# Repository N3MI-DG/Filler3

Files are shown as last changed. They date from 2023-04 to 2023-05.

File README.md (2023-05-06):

# Filler3
 Open source can filler built from 3D printer, 3D printed and common home brewing items.

 Credits to <a href="https://www.youtube.com/channel/UCIIYTzYpd8D7y816diZB0Dw">HarryBrew69</a> for coming up with the idea of using an Arduino to run a can filler and sense fill level via analog inputs. And <a href="https://github.com/kloon/OpenBeerFiller">kloon</a> for his original implimentation of Harry's idea.

<a href="BOM.csv">BOM</a><br/>
<a href="/Build/">The Build</a><br/>
<a href="/Photos/">Build Photos</a><br/>
<a href="/firmware/">Firmware</a><br/>
<a href="/CQ-SRC/">CadQuery</a><br/>
<br/>

## Method of operation
<p>
    When plugged in the can filler will move the servo to the <b>SERVO_POS_IDLE</b> position, make sure the gas solenoid is disabled and raise the gantry to its home position and wait for user input.
    <br/><br/>
    Pressing the button will activate the filling process. 
    <br/><br/>
    The gantry will move to the <b>PRE_PURGE_POSITION</b> and activate the gas solenoid for the <b>PRE_PURGE_DURATION</b>.
    <br/><br/>
    After purging the gantry will move to the <b>FILL_POSITION</b>, the servo will move to the <b>SERVO_POS_FILL</b> position and the LED will start "breathing" to indicate the can is filling. 
    <br/><br/>
    If using <b>POSITIVE_PRESSURE</b> mode, the purge cap should be touching the can while filling. If not using the <b>POSITIVE_PRESSURE</b> mode, the purge cap should be positioned as close to the can as possible without touching. 
    <br/><br/>
    While filling the sensor wire is constantly being read and checking if the analog input has gone past the <b>SENSOR_TRIGGER</b> value.
    The <b>SENSOR_TRIGGER</b> value will need to be tuned if canning non still liquids.
    <br/><br/>
    Once full the servo will move back to the <b>SERVO_POS_IDLE</b> position. While the can is full and the gantry is down, the combination of <b>POSITIVE_PRESSURE</b> and <b>POST_PURGE_DURATION</b> settings will determine what happens next.
    <br/><br/>
    If using <b>POSITIVE_PRESSURE</b> mode, the LED will start "blinking" to indicate the can is full and wait for the button to be pressed before moving to the next position. This behaviour is to allow the user to grab hold of the can before the gantry moves to the next position. If the gantry moves while the purge cap is touching the can and the can is not held in position things can get very messy.
    <br/><br/>
    If <b>POSITIVE_PRESSURE</b> mode is disabled, the gantry will automatically move to the next position once the can is full. 
    <br/><br/>
    If a <b>POST_PURGE_DURATION</b> value has been set the gantry will move to the <b>POST_PURGE_POSITION</b> and activate the purge solenoid for the <b>POST_PURGE_DURATION</b> before moving the gantry back to the home position.
    <br/><br/>
    If no <b>POST_PURGE_DURATION</b> is set the gantry will move directly to the home position after filling.
    <br/><br/><br/>
    <b>NOTE: IF THE BUTTON IS PRESSED ANY TIME OTHER THAN WHILE THE GANTRY IS AT ITS HOME POSITION OR WHILE THE LED IS "BLINKING" IT IS TREATED AS AN EMERGENCY STOP AND WILL RESET THE FILLER.</b>
</p>
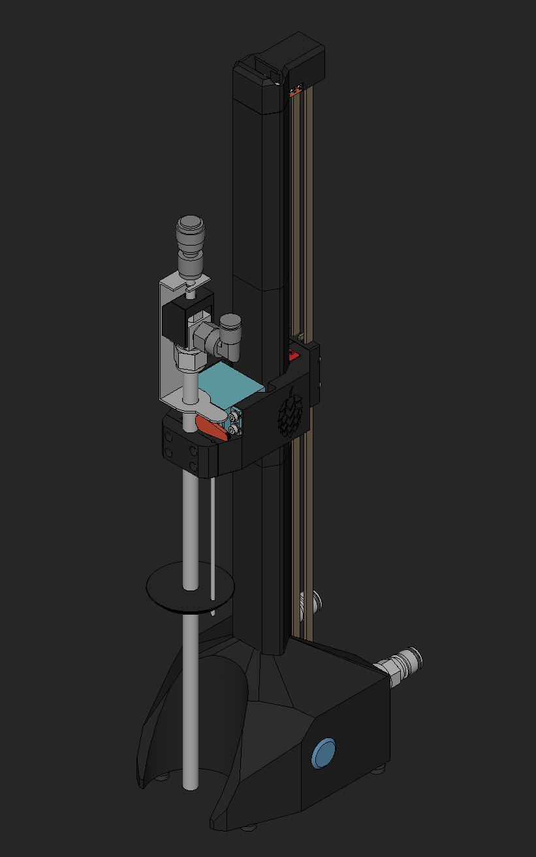
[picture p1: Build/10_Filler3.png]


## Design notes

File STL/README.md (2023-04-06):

# Printed Parts

1x Base.stl<br/>
1x Car Stop.stl<br/>
1x Carriage.stl<br/>
1x Condensation Cover.stl<br/>
1x DFU Helper.stl<br/>
1x Filler Mount Front.stl (PETG Recommended for clamping purpose.)<br/>
1x Filler Mount Left.stl (PETG Recommended for clamping purpose.)<br/>
1x Filler Mount Right.stl (PETG Recommended for clamping purpose.)<br/>
4x Foot.stl<br/>
1x Handle Stop.stl<br/>
1x Idle Stop.stl<br/>
1x Motor Mount.stl (PETG/ABS/ASA Recommended for heat absorbtion.)<br/>
1x PCB Spacer.stl<br/>
1x Purge Cap.stl (FLEXIBLE Required to push fit.)<br/>
2x Tube Section.stl<br/>

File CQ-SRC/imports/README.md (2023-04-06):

Note: Some files were modified from their originals to either simplify them or suit this project. The URLs listed are the original source.
<br/>

* 17HS08-1004S.stp : https://grabcad.com/library/17hs08-1004s-4-lead-nema-17-stepper-motor-1<br/>
* ball_lock.dxf : David Gray / Filler3<br/>
* dfu_a.dxf : David Gray / Filler3<br/>
* dfu_b.dxf : David Gray / Filler3<br/>
* EBB42.step : https://github.com/bigtreetech/EBB/blob/master/EBB%20CAN%20V1.1%20(STM32G0B1)/EBB42%20CAN%20V1.1/3D/BIGTREETECH%20EBB42%20CAN%20V1.1.step<br/>
* filler_clearance.dxf : David Gray / Filler3<br/>
* filler_tube.step : David Gray / Filler3<br/>
* hop_cone.step : David Gray / Filler3<br/>
* MG996R.step : https://grabcad.com/library/tower-pro-mg-996r-motor-3d-model-1<br/>
* MGN12_RAIL_400.step : https://grabcad.com/library/mgn12-lineer-guide-1<br/>
* MGN12H_CAR.step : https://grabcad.com/library/mgn12-lineer-guide-1<br/>
* pulley.dxf : David Gray / Filler3<br/>
* servo_arm.step : David Gray / Filler3<br/>
* Solenoid_Valve_1_4.stp : https://grabcad.com/library/china-solenoid-valve-1-4-for-reference-1<br/>
* SPDT.stp : https://grabcad.com/library/microswitch-13<br/>
* v_inner_a.dxf : David Gray / Filler3<br/>
* v_inner_b.dxf : David Gray / Filler3<br/>
* v_inner_c.dxf : David Gray / Filler3<br/>
* v_inner_d.dxf : David Gray / Filler3<br/>
* V_tube_body.dxf : David Gray / Filler3<br/>
* V-Slot 20x20.dxf : https://github.com/richard-scott/OpenBuilds<br/>

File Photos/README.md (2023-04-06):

# Photos

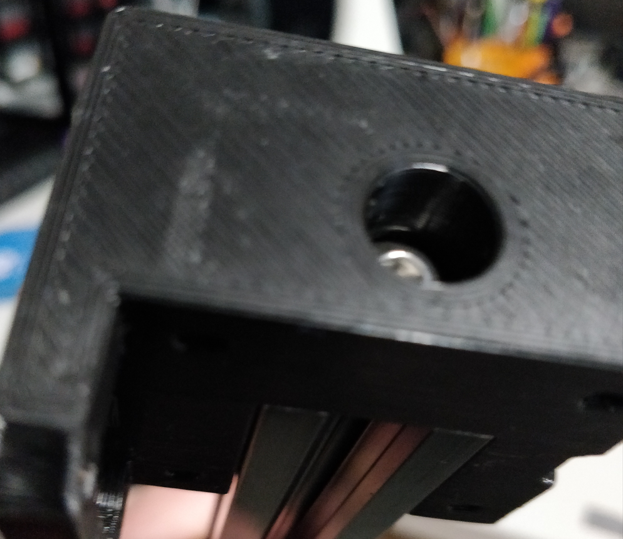
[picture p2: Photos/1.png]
<br/>
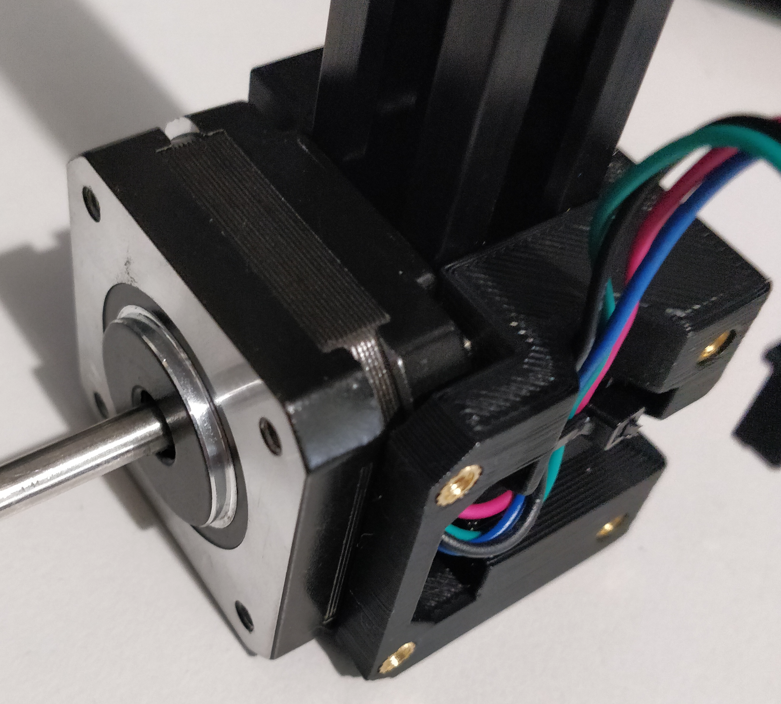
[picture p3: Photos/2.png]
<br/>
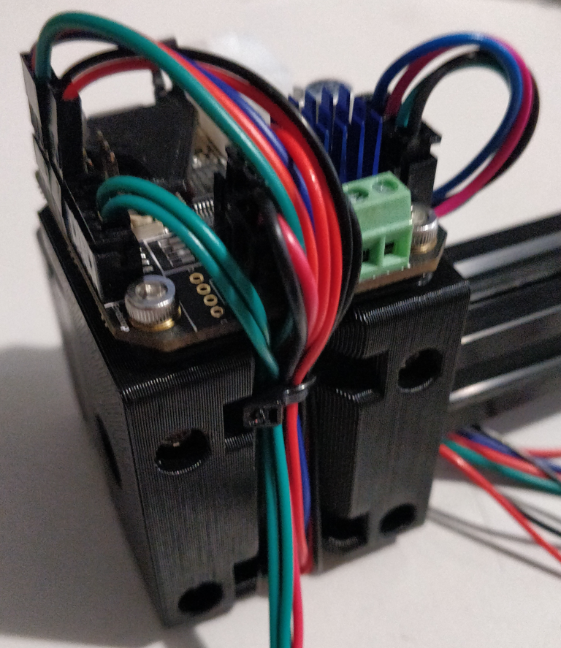
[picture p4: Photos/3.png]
<br/>
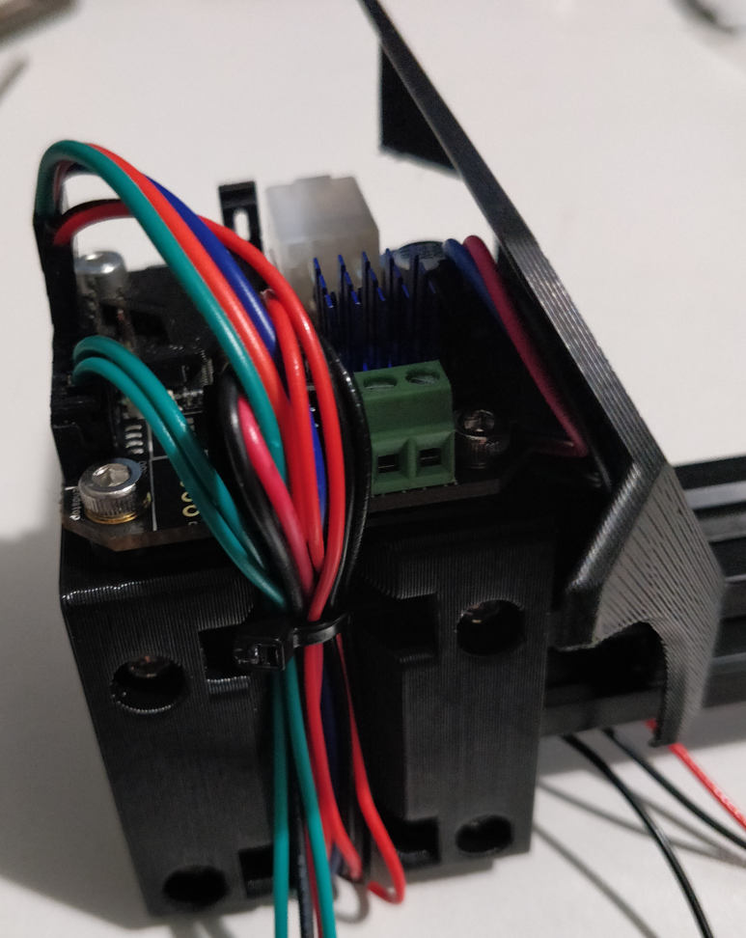
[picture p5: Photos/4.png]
<br/>
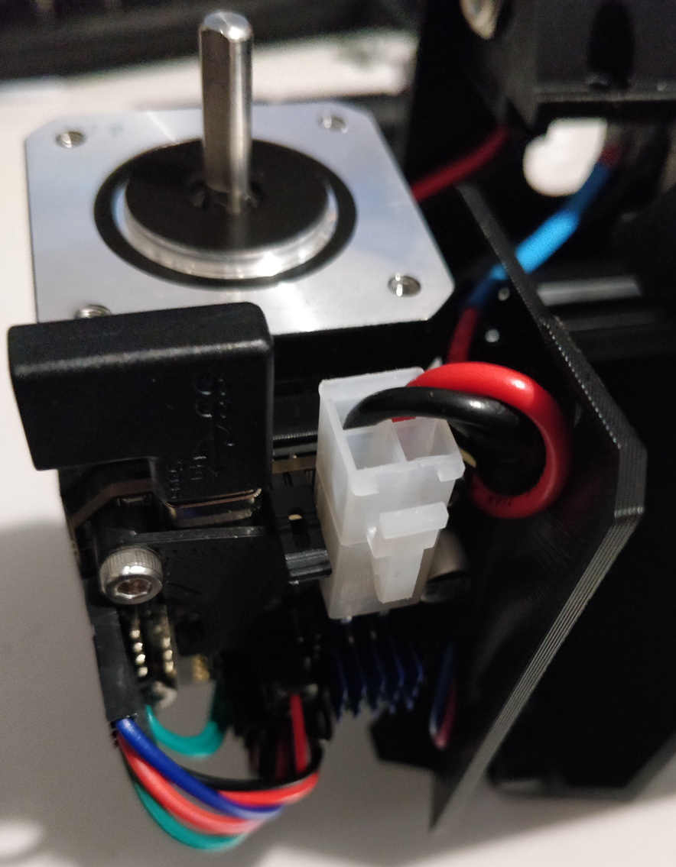
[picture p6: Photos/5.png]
<br/>
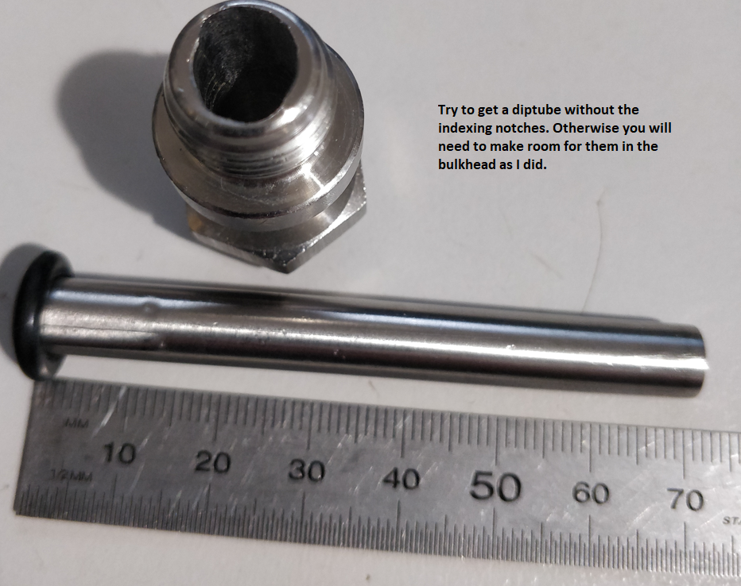
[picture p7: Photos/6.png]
<br/>
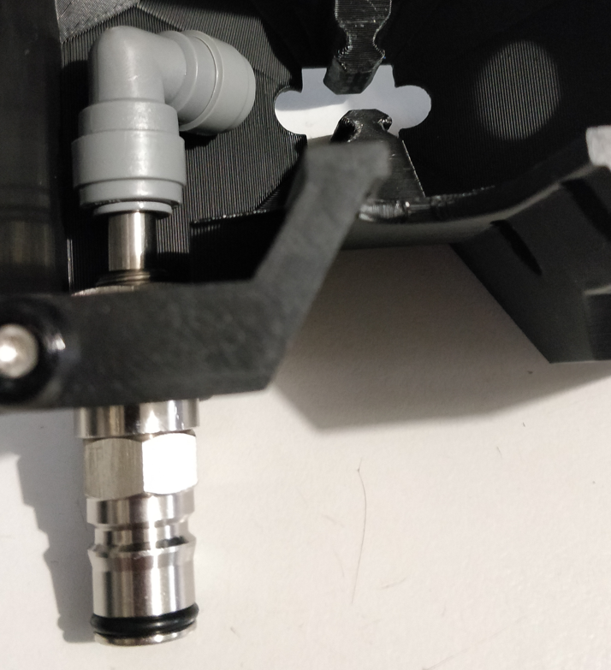
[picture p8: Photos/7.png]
<br/>
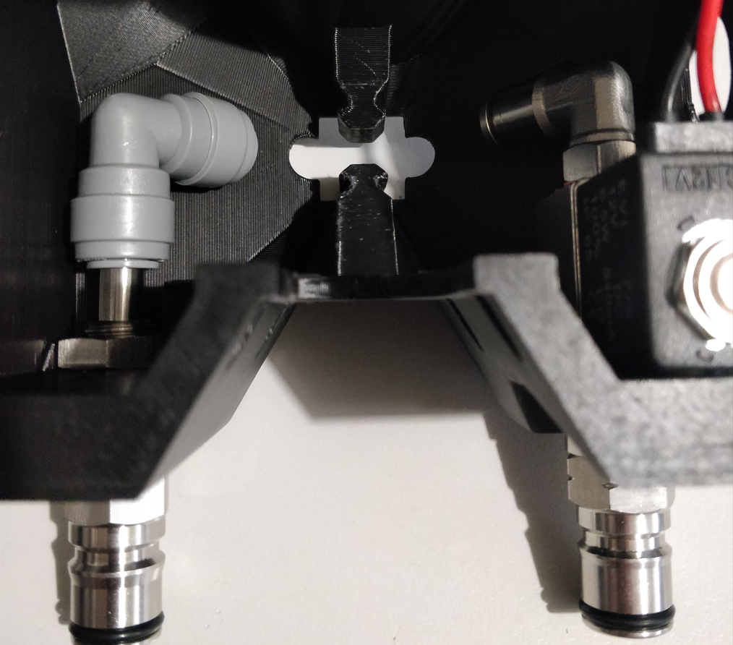
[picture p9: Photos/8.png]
<br/>
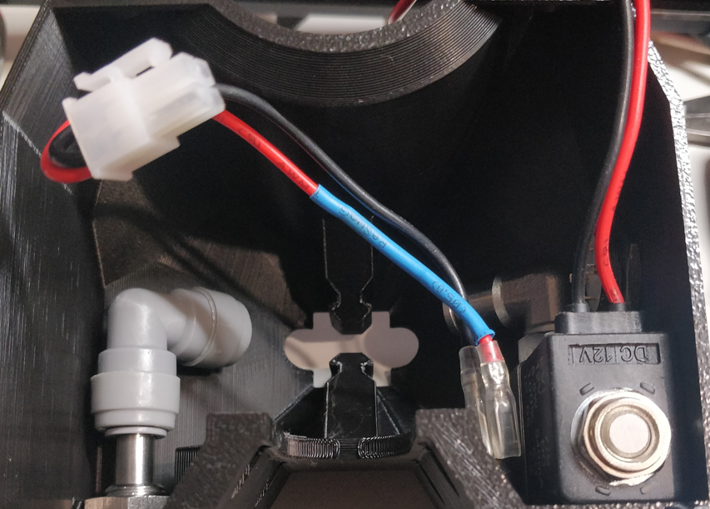
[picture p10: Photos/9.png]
<br/>
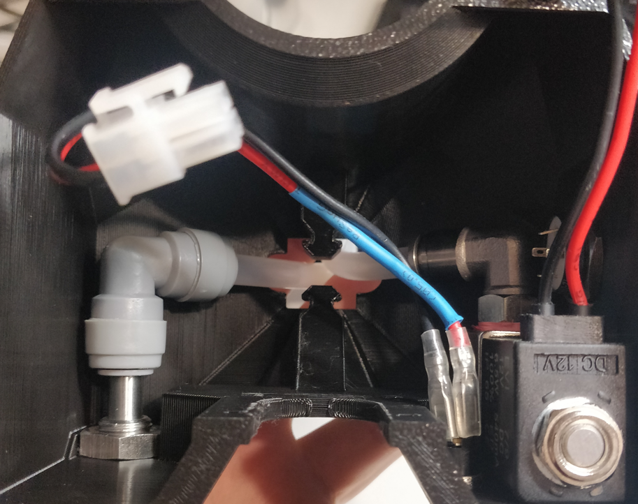
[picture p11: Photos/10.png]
<br/>
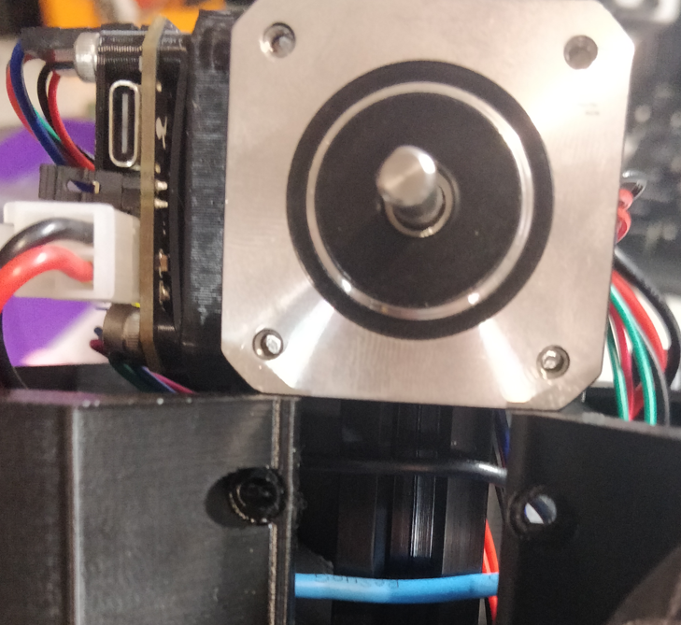
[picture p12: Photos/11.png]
<br/>
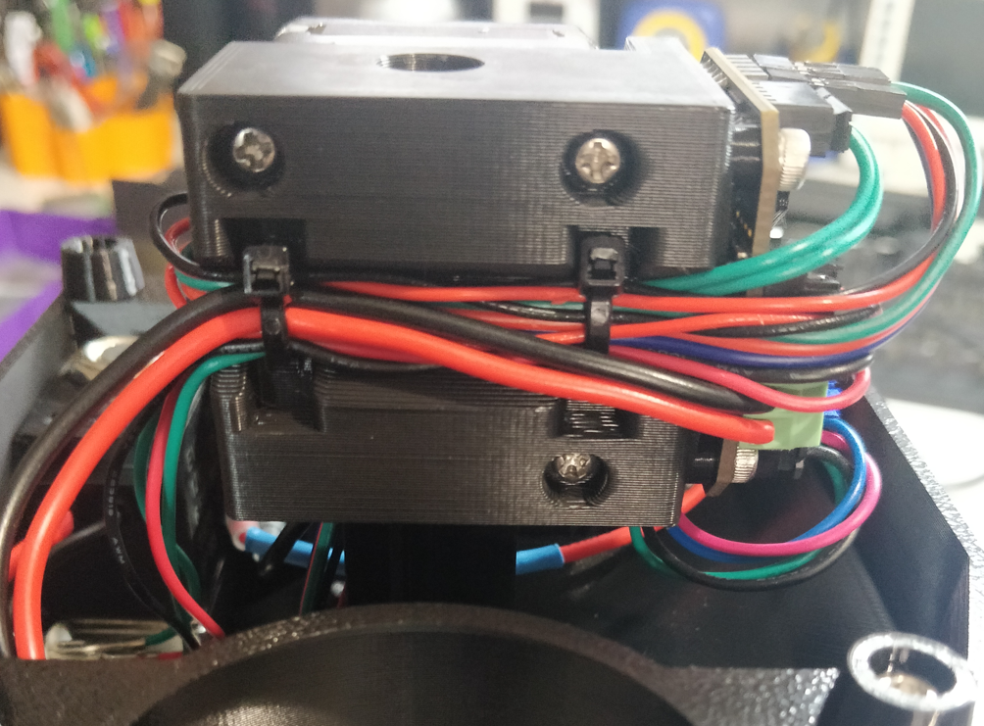
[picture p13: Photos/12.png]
<br/>
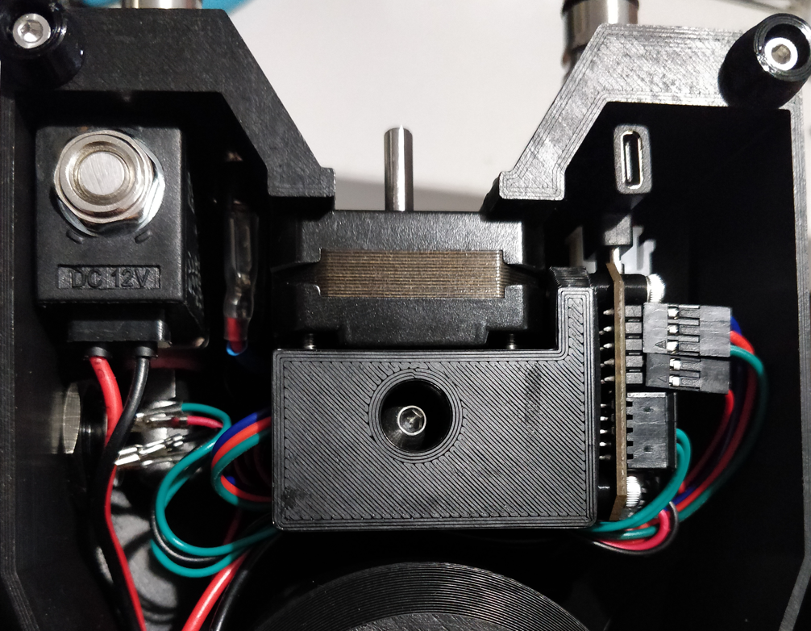
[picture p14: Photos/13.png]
<br/>
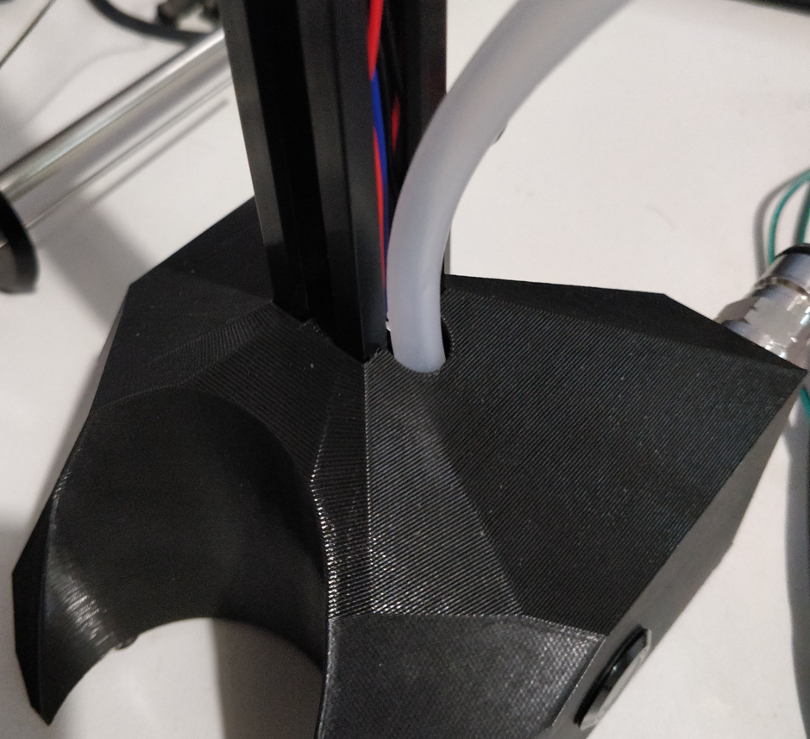
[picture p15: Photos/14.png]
<br/>
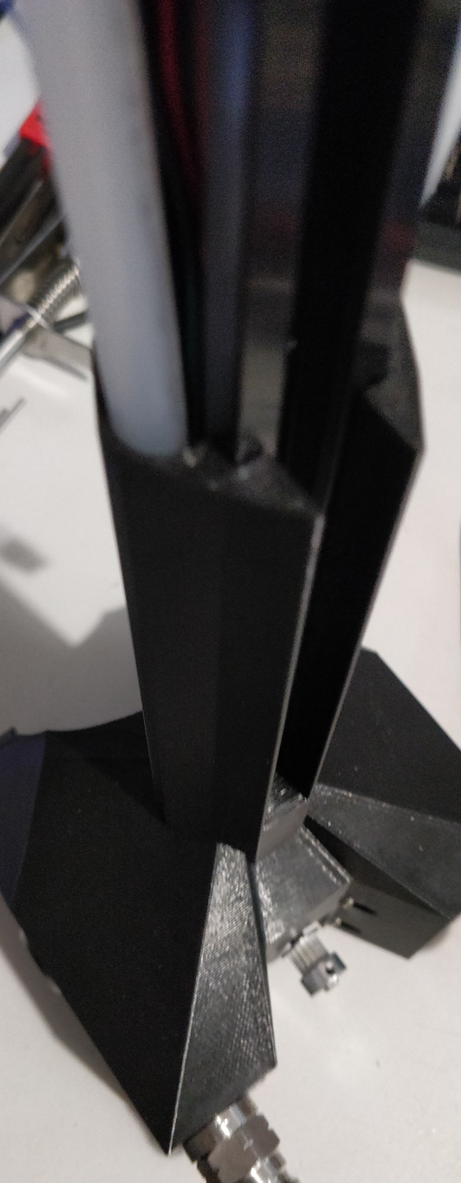
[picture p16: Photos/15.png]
<br/>
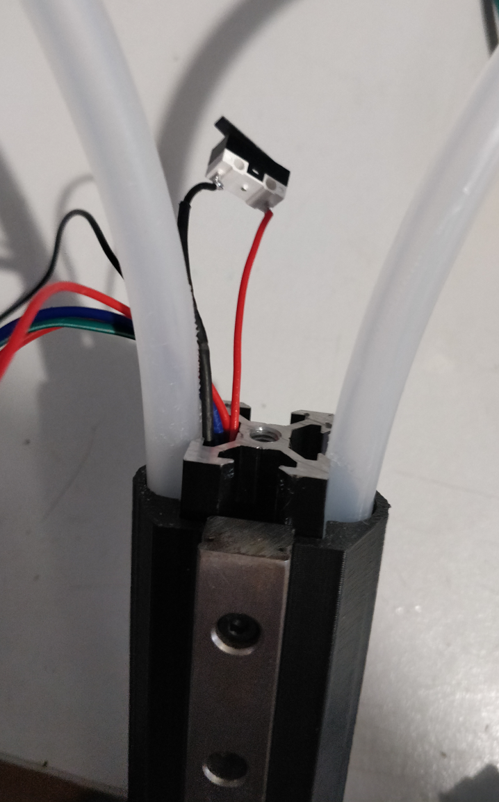
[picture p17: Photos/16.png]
<br/>
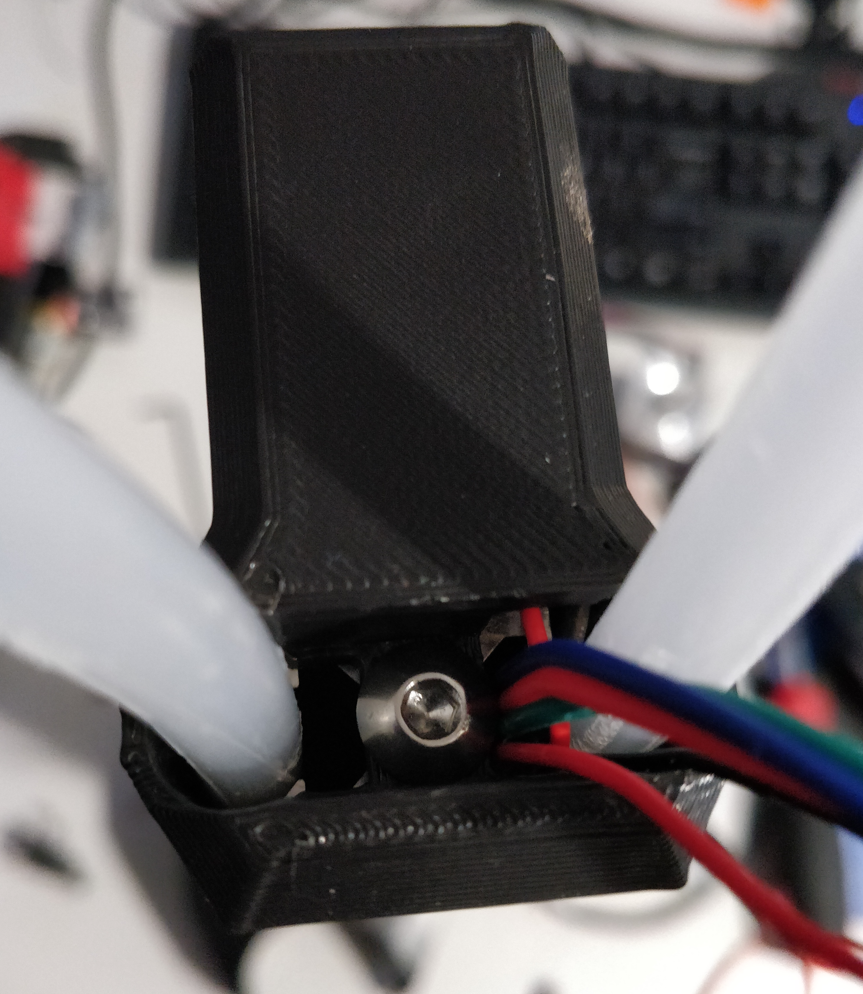
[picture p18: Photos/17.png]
<br/>
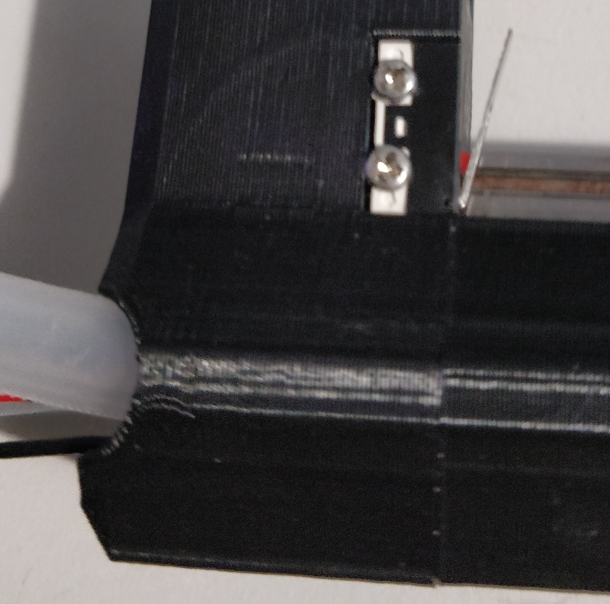
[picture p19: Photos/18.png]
<br/>
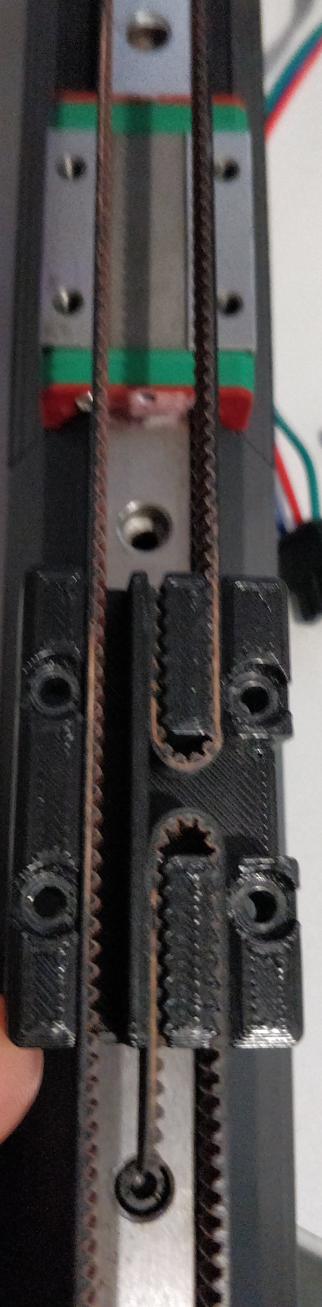
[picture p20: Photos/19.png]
<br/>
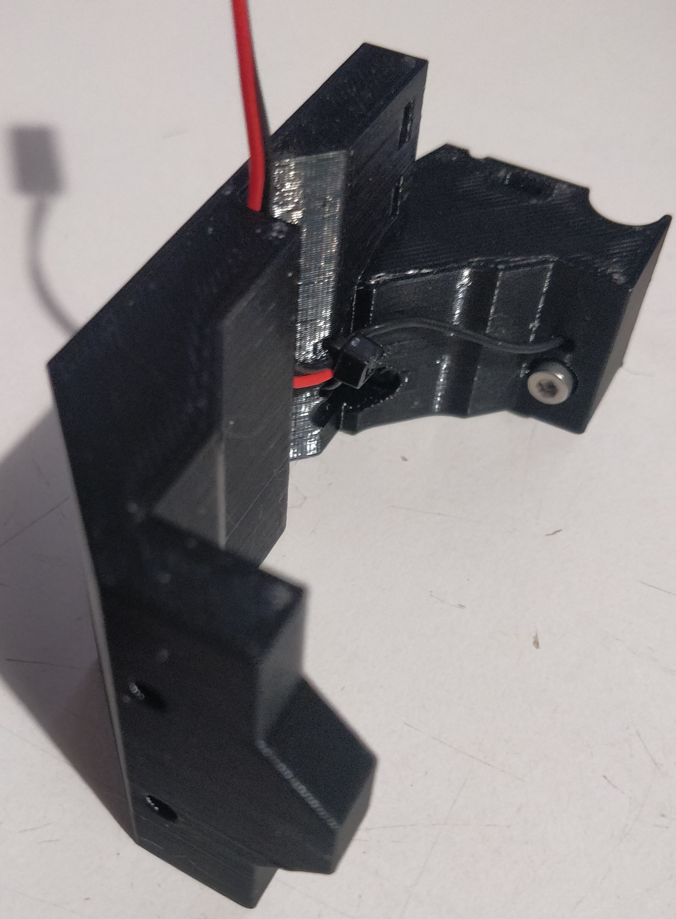
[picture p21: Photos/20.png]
<br/>
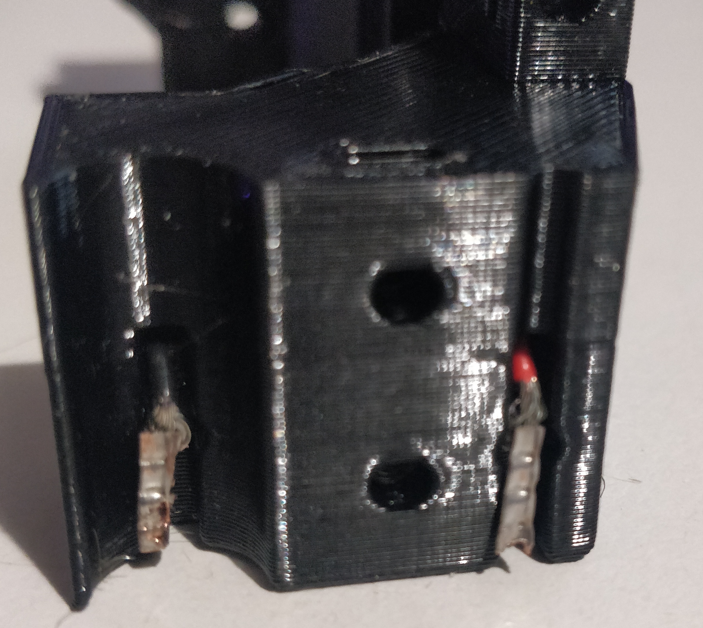
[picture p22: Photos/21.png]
<br/>
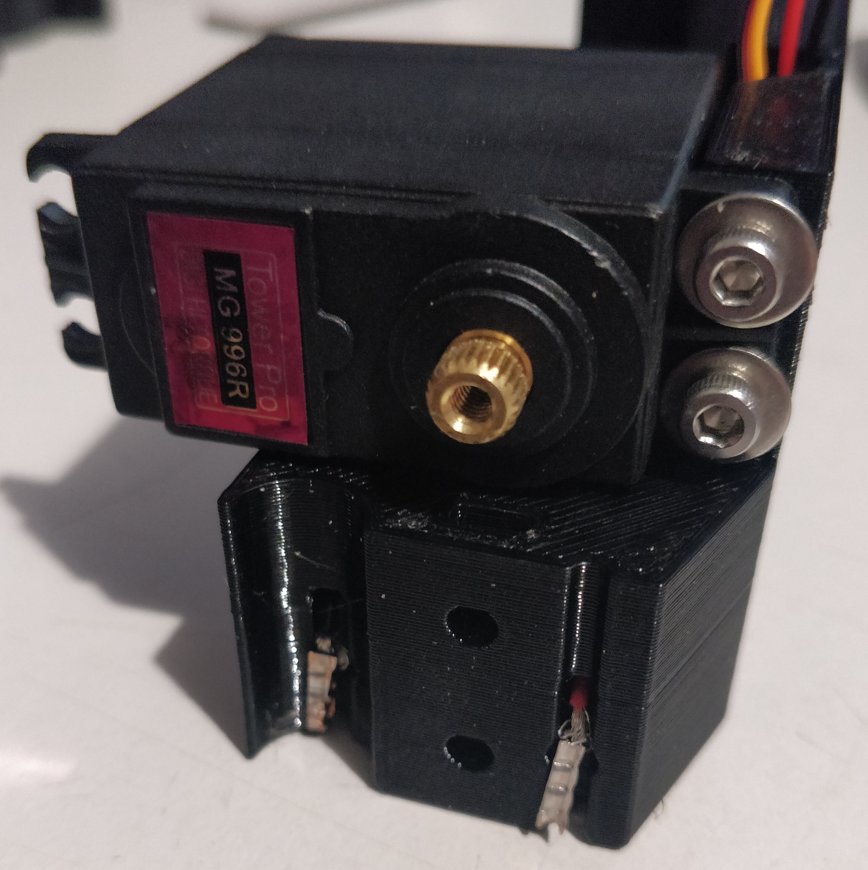
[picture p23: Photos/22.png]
<br/>
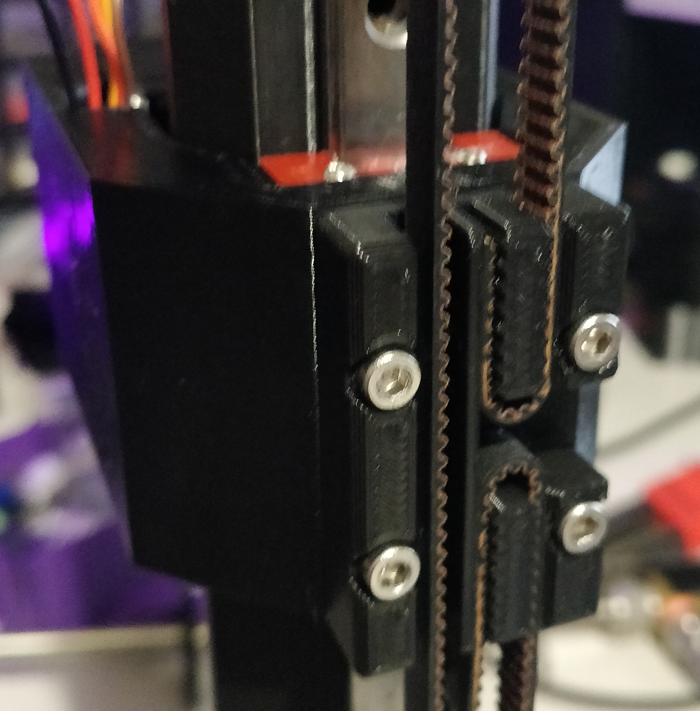
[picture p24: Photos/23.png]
<br/>
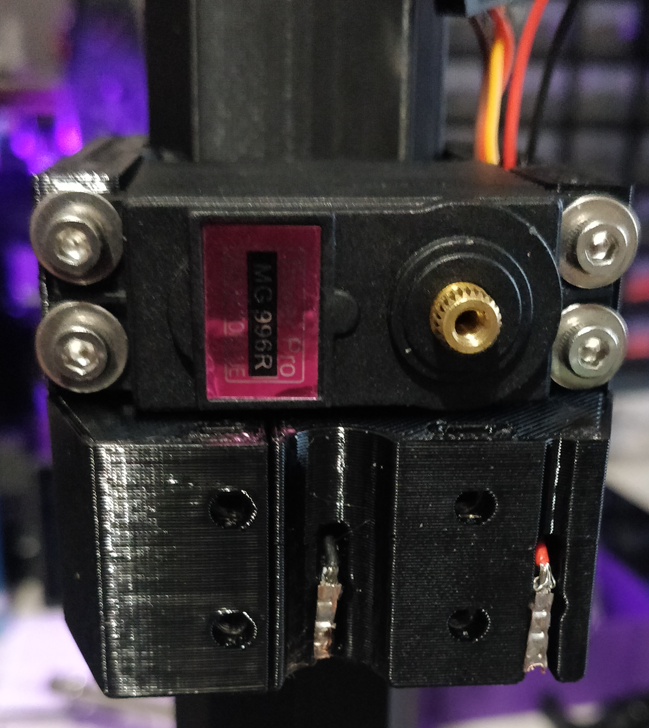
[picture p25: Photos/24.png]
<br/>
<br/>
<br/>
<br/>

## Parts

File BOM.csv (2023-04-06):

Item | QTY | Hyperlink | Option 1 | Option 2
Stepper Motor 17HS08-1004S | 1 | https://www.aliexpress.com/item/32585429251.html
GT2 Pulley 16T | 1 | https://www.aliexpress.com/item/1005002226516848.html | 16 Teeth Bore 5mm | 6mm Width
EBB42 3D Can Bus Board | 1 | https://www.aliexpress.com/item/1005004242828520.html | EBB42 CAN
USB C 90 Degree Elbow | 1 | https://www.aliexpress.com/item/1005002755168110.html | Elbow Typec F to M
20x20 V Slot Extrusion | 1 | https://www.makerstore.com.au/product/black-v-slot-20-x-20mm/ | 500mm
19mm Momentary Switch | 1 | https://www.aliexpress.com/item/1005003862203895.html | 12-24V LED Momentary | 19mm
Ball Lock Bulkhead (Liquid) | 1 | https://www.kegland.com.au/ball-lock-post-with-1-4-inch-bulkhead-assembly-liquid.html
Dip Tube (Liquid) | 1 | https://www.kegland.com.au/stainless-keg-dip-tube-long-liquid.html
90 Degree Duotight Elbow (8mm) | 1 | https://www.kegland.com.au/duotight-8mm-push-in-tee-piece-double-oring-897.html
Ball Lock Bulkhead (Gas) | 1 | https://www.kegland.com.au/ball-lock-post-with-1-4-inch-bulkhead-assembly-gas.html
Gas Solenoid | 1 | https://www.aliexpress.com/item/1005003324287626.html
Push Fit/Male Thread Elbow | 1 | https://www.aliexpress.com/item/1005001357072469.html | PL8-02
DC099 5.5 x 2.1mm Power Socket | 1 | https://www.aliexpress.com/item/4000053061172.html
MGN12H Rail and Carriage | 1 | https://www.aliexpress.com/item/4000264234020.html | 400mm | MGN12H
Microswitch 13x9.5 | 1 | https://www.aliexpress.com/item/4000029868541.html
GT2 Idler Pulley | 1 | https://www.aliexpress.com/item/32796878074.html | Bore 3mm No Teeth | For width 6mm-Silver
MG996R Servo | 1 | https://www.aliexpress.com/item/1005004556540857.html | MG996R - 180 Degrees | All Metal
GT2 Timing Belt | 1 | https://www.aliexpress.com/item/32853559638.html | 2M-6MM-GT2
Beer Gun Filler (duotight as it comes with hose) | 1 | https://www.kegland.com.au/duotight-bottle-filler-beer-gun.html
Push Fit/Female Thread Elbow | 1 | https://www.aliexpress.com/item/33011074542.html | 8mm OD Hose | 1 / 4 “
Duotight reducer 8mm-6.35mm | 1 | https://www.kegland.com.au/duotight-6-5mm-1-4-x-8mm-5-16-reducer.html
2.4mm Stainless TIG Wire or 2.5 Rod | 1 | https://www.aliexpress.com/item/4000186787300.html | 2.5mm
5.5 x 2.1mm Barrel Jack 12V 1.25A+ Power Supply
M2x10 Pan Head Self Tapper Screw | 2
M3X6 Cap Head Screw | 8
M3x10 Cap Head Screw | 16
M3x16 Cap Head Screw | 1
M3x20 Cap Head Screw | 6
M3x40 Pan Head Screw | 3 | Included with the EBB42
M3 Washer | 8
M3 T Nut | 4
M3 Square Nut | 10
M3 Brass Heatset Inserts - Short M3x5x4 | 8
M5x10 Button Head Screw | 2

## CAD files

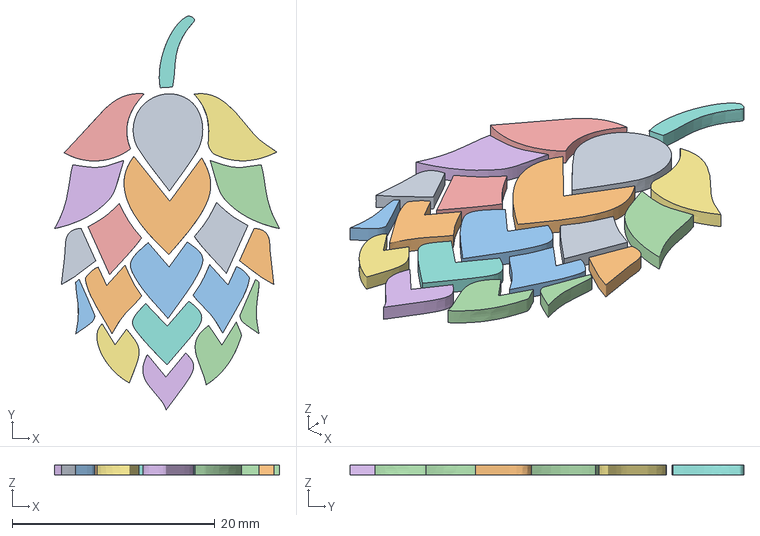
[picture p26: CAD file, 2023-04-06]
CQ-SRC/imports/hop_cone.step
22.2 x 38.8 x 1.00 mm

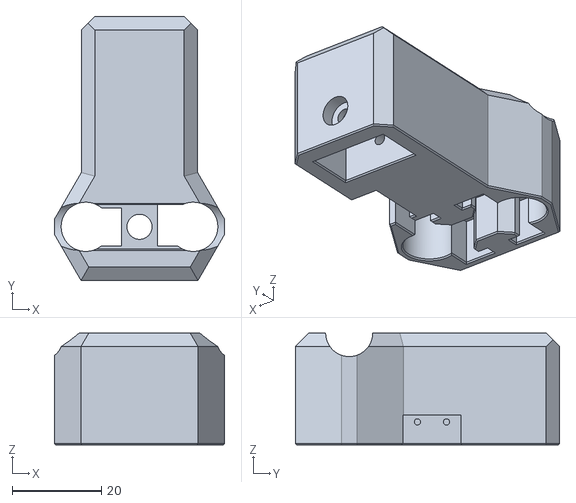
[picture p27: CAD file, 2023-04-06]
STL/Idle Stop.stl
38.0 x 59.0 x 25.0

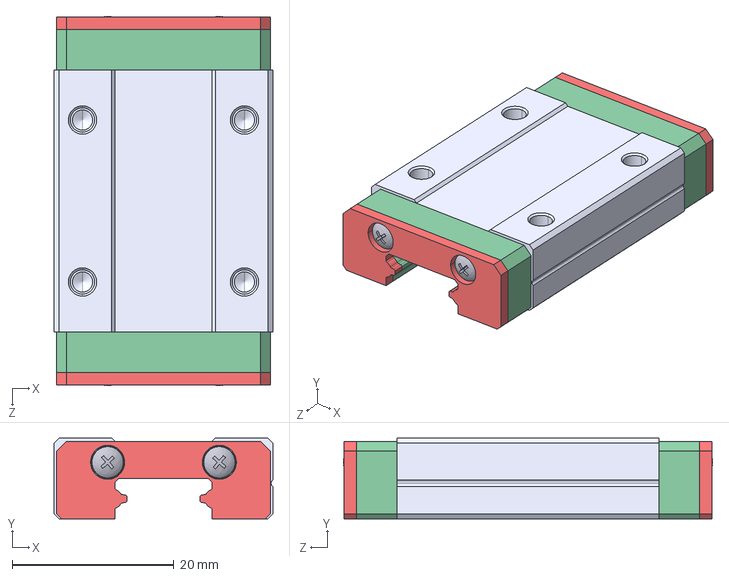
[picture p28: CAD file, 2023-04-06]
CQ-SRC/imports/MGN12H_CAR.step
27.0 x 10.0 x 45.6 mm

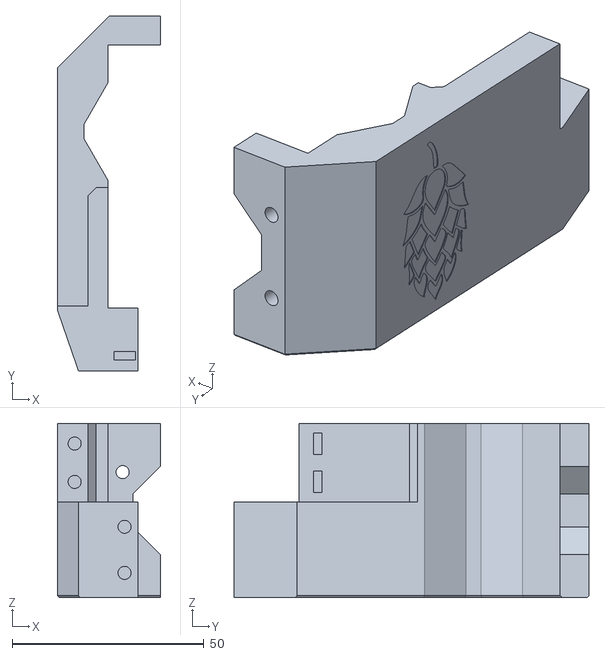
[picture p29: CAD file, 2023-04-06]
STL/Filler Mount Left.stl
26.9 x 92.5 x 45.4

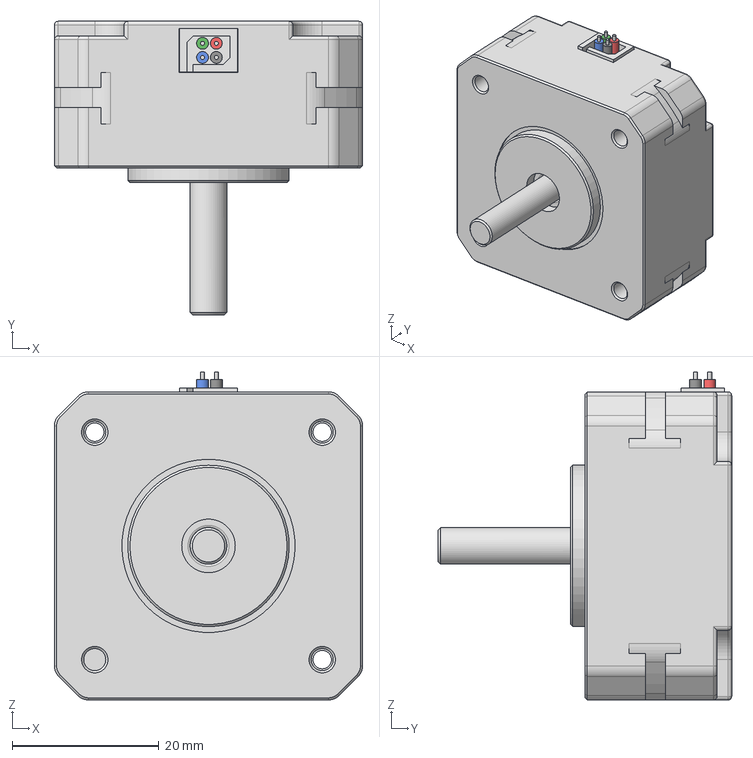
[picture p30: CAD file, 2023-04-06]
CQ-SRC/imports/17HS08-1004S.stp
42.0 x 40.0 x 44.7 mm

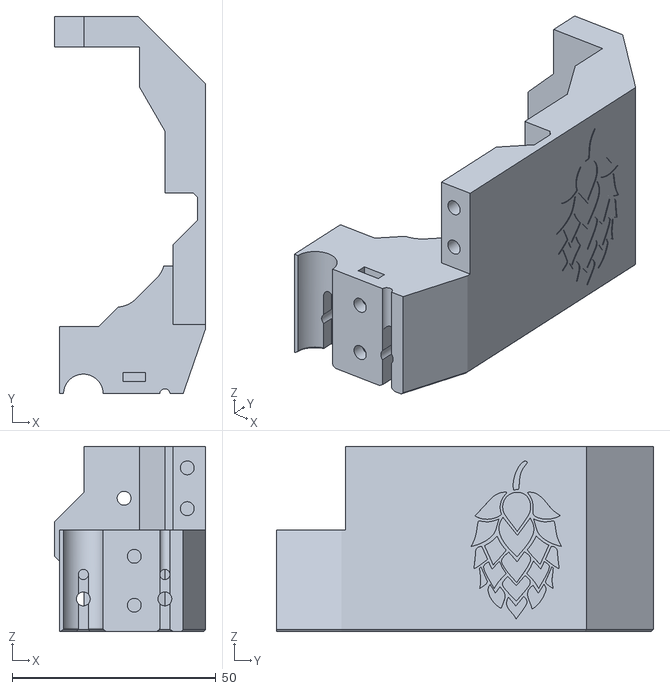
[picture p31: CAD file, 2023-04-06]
STL/Filler Mount Right.stl
37.1 x 92.5 x 45.4

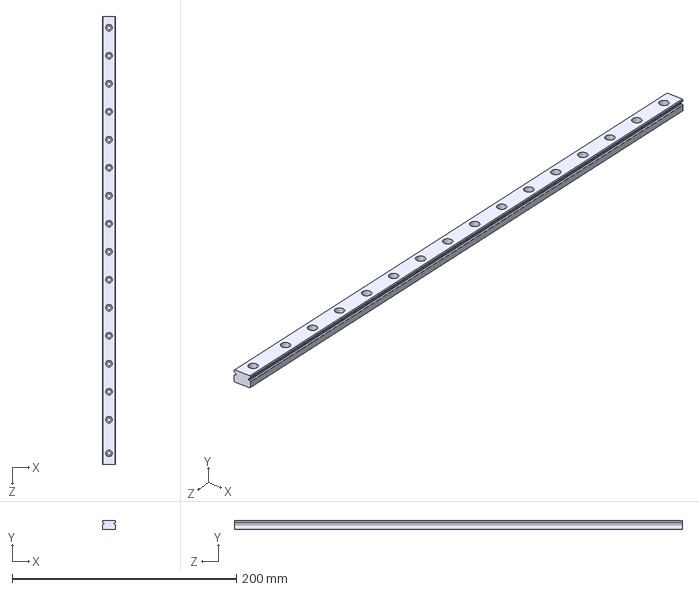
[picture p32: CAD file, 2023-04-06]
CQ-SRC/imports/MGN12_RAIL_400.step
12.0 x 8.00 x 400.0 mm

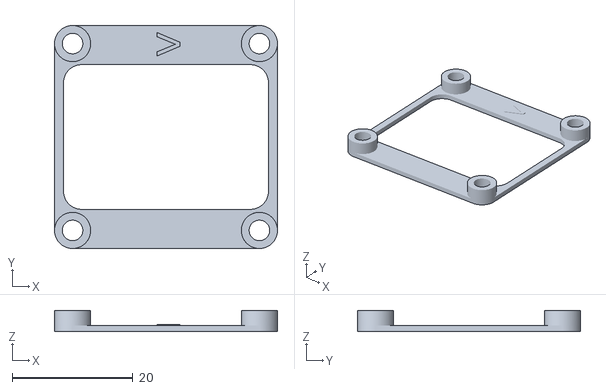
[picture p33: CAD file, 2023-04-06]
STL/PCB Spacer.stl
37.0 x 37.0 x 3.50

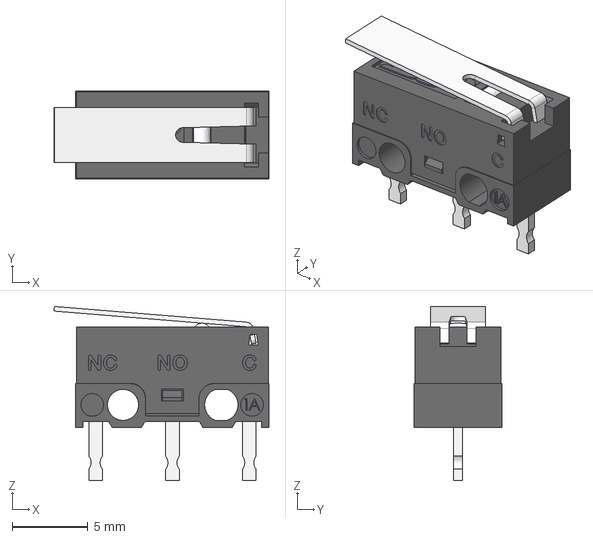
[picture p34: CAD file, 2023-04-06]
CQ-SRC/imports/SPDT.stp
14.2 x 5.80 x 11.5 mm

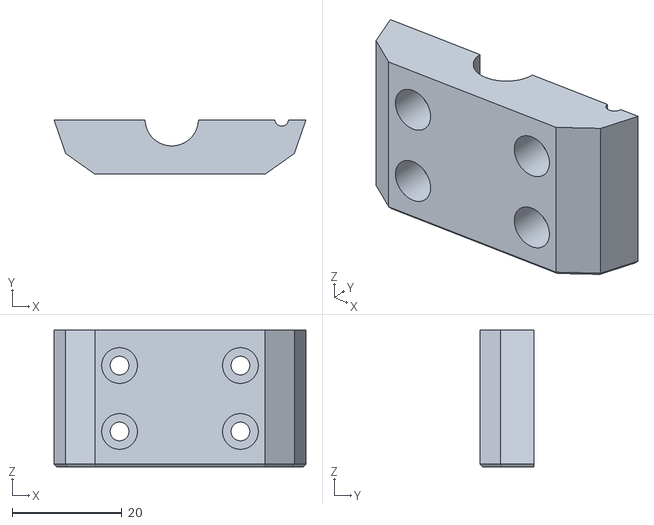
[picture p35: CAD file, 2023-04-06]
STL/Filler Mount Front.stl
45.9 x 9.90 x 24.9

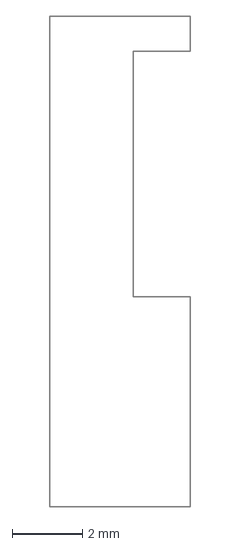
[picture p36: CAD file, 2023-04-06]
CQ-SRC/imports/pulley.dxf
4.00 x 14.0 mm

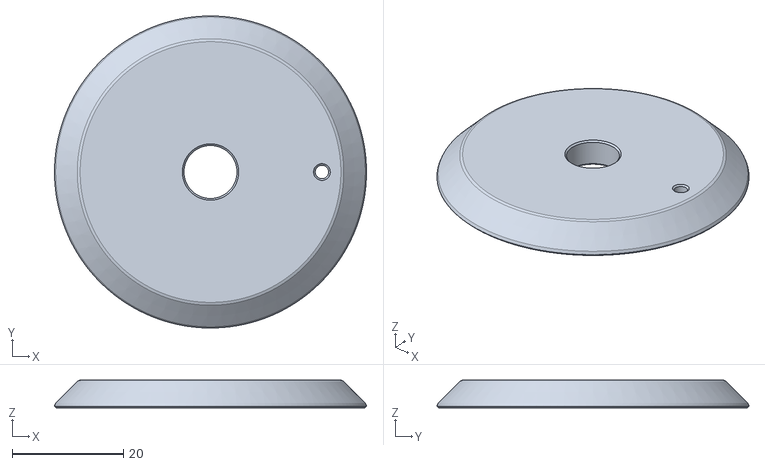
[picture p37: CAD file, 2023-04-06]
STL/Purge Cap.stl
56.0 x 56.0 x 5.00

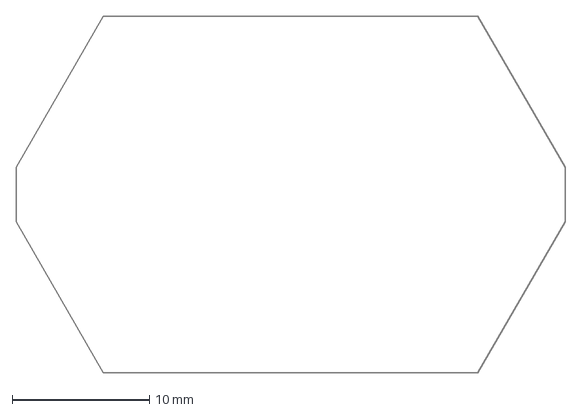
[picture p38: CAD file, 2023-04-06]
CQ-SRC/imports/filler_clearance.dxf
40.0 x 26.0 mm

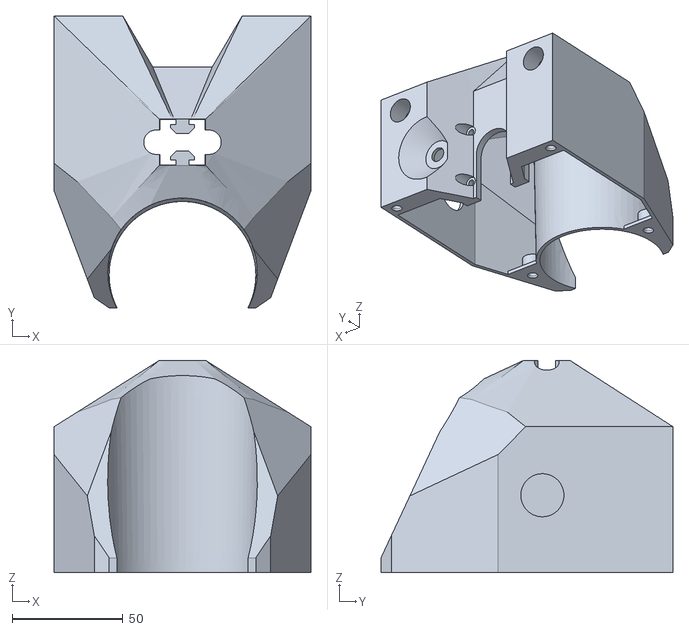
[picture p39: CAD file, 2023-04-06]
STL/Base.stl
116.2 x 132.1 x 96.0

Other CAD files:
CQ-SRC/imports/servo_arm.step
STL/Condensation Cover.stl
CQ-SRC/imports/filler_tube.step
STL/Handle Stop.stl
CQ-SRC/imports/MG996R.step
CQ-SRC/imports/Solenoid_Valve_1_4.stp
CQ-SRC/imports/V-Slot 20x20.dxf
CQ-SRC/imports/V_inner_a.dxf
CQ-SRC/imports/V_inner_b.dxf
CQ-SRC/imports/V_inner_c.dxf
CQ-SRC/imports/V_inner_d.dxf
CQ-SRC/imports/V_tube_body.dxf
CQ-SRC/imports/ball_lock.dxf
CQ-SRC/imports/dfu_a.dxf
CQ-SRC/imports/dfu_b.dxf
STL/Car Stop.stl
STL/Carriage.stl
STL/DFU Helper.stl
STL/Foot.stl
STL/Motor Mount.stl
STL/Tube Section.stl

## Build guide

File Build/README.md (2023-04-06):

# The Build 

### Electrical Preperations
* Trim stepper motor cable to be 90mm long and crimp to suit EBB42 Motor connector.
* Trim solenoid cable to be 190mm long.
* Crimp 150mm long switch NO and COM wires to suit EBB42 Endstop connector (PB6, GND) and crimp the other end to suit switch.
* Crimp 150mm long switch LED wires to suit EBB42 FAN1 connector (VIN, PA0) and crimp the other end to suit switch.
* Crimp 1060mm long sensor wires to suit EBB42 TH0 connector (GND, PA3) (Optional but recommended to add a connector at the filler mount end).
* Crimp 1080mm long servo wires to suit EBB42 Probe Connector (GND, +5V, PB9) and solder 2.54 header on the other end (Optional but recommended to add a connector at the filler mount end).
* Crimp 660mm long endstop wires to suit EBB42 Probe Connector (GND, PB8).
* Crimp 150mm long power wires to suit EBB42 CAN connector (GND, VIN) and crimp other end to suit DC jack.
* Apply the EBB42 stepper motor heatsink and install the VBUS jumper.

### Tube Preperations
* Cut a piece of 8mm OD tube 770mm long for the beer line.
* Cut a piece of 8mm OD tube 815mm long for the gas line.

### 3D Print Preperations
* Install 4 off M3 threaded inserts into base.stl.
* Install 4 off M3 threaded inserts into motor_mount.stl.

### Dip Tube Preperations
* Cut down a keg dip tube to 70mm long. Preferably 1 without the liquid centering notches or you will need to also notch out the liquid bulkhead fitting as I did.

<br/>

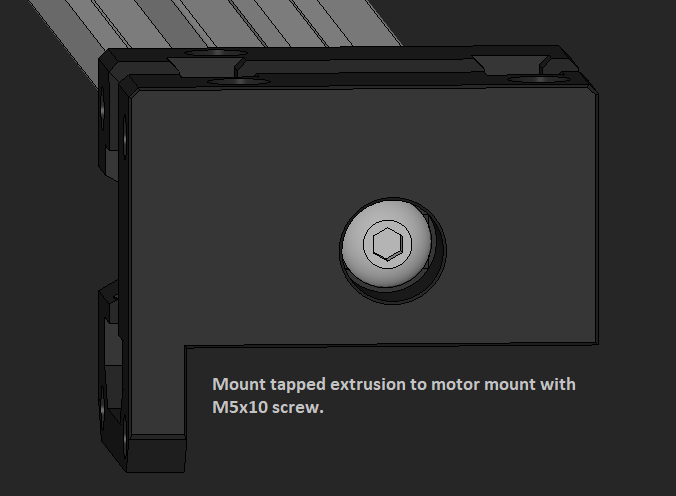
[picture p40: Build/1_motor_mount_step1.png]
<br/>
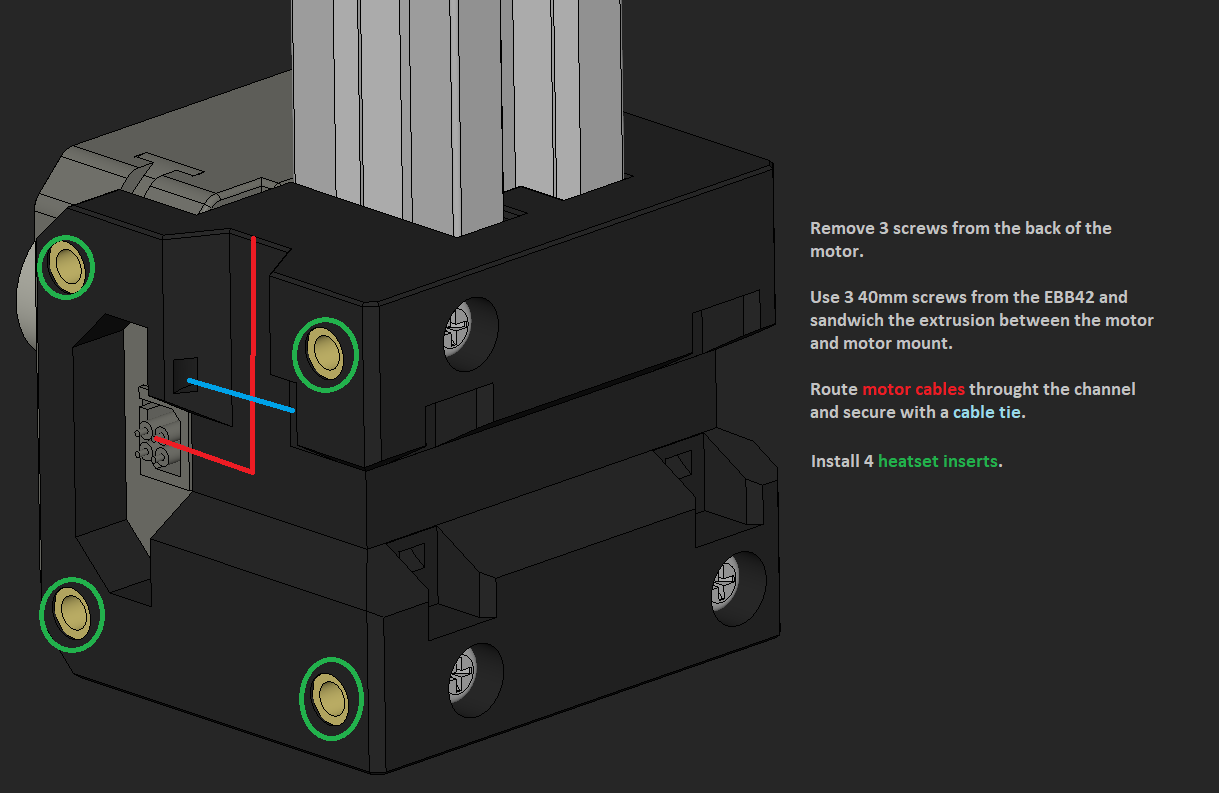
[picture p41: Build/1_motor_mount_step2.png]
<br/>
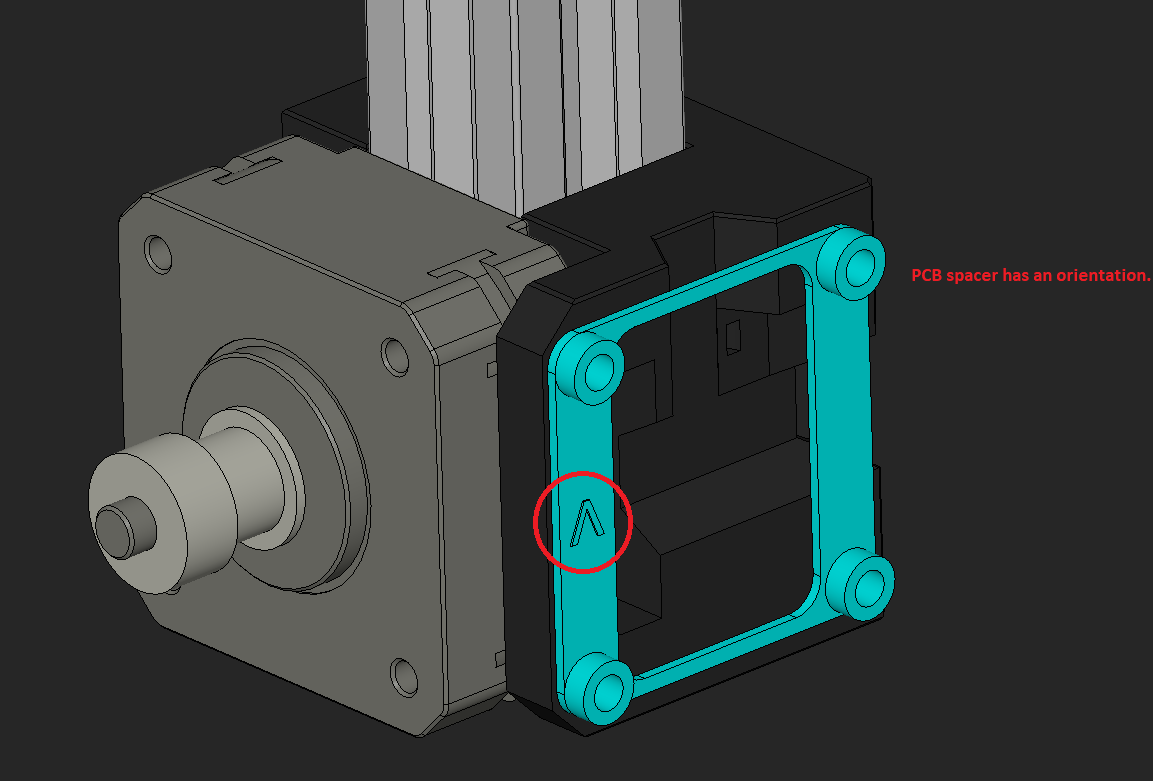
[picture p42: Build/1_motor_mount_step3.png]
<br/>
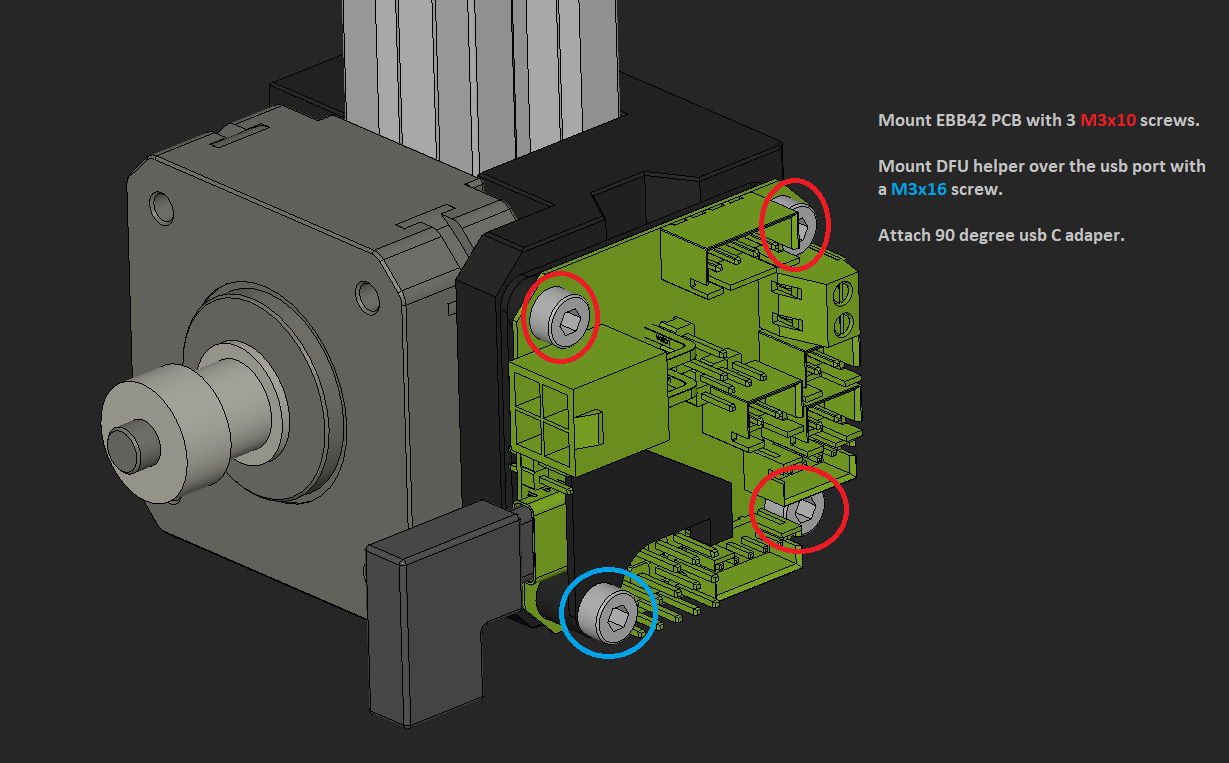
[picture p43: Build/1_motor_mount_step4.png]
<br/>
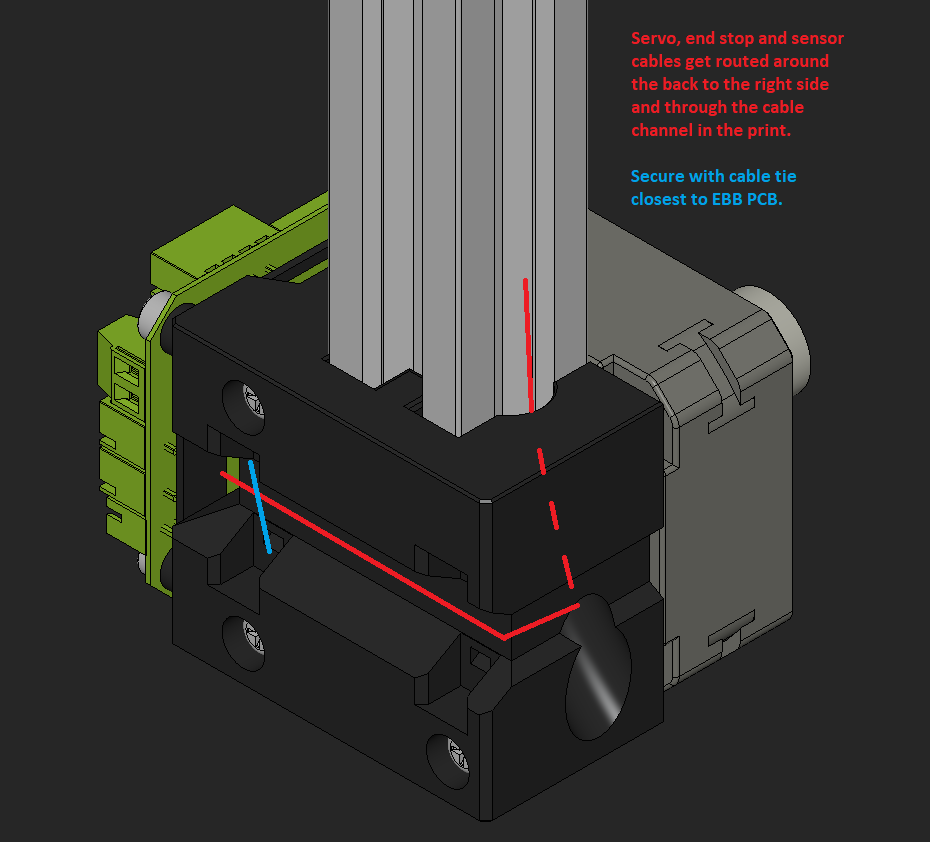
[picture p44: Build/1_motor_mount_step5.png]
<br/>
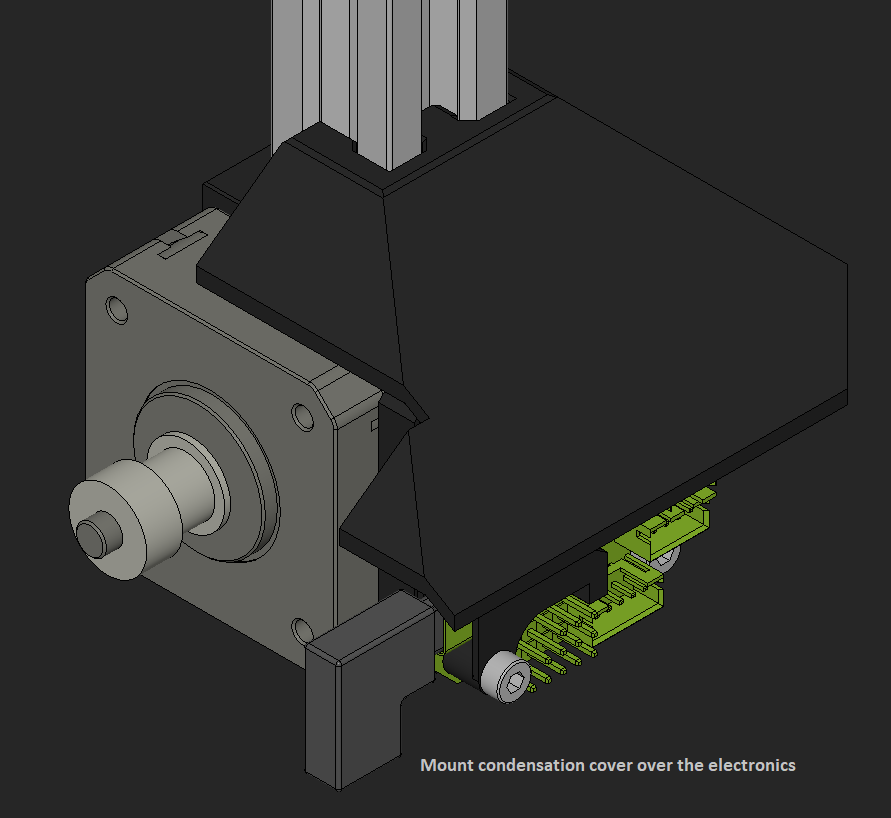
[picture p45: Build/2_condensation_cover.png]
<br/>
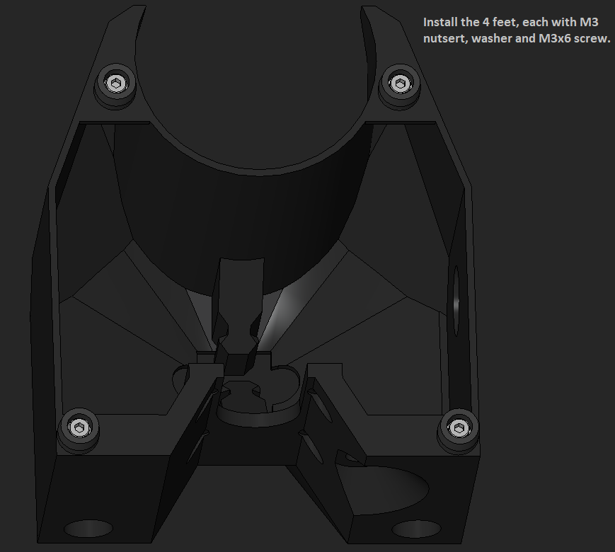
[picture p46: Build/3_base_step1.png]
<br/>
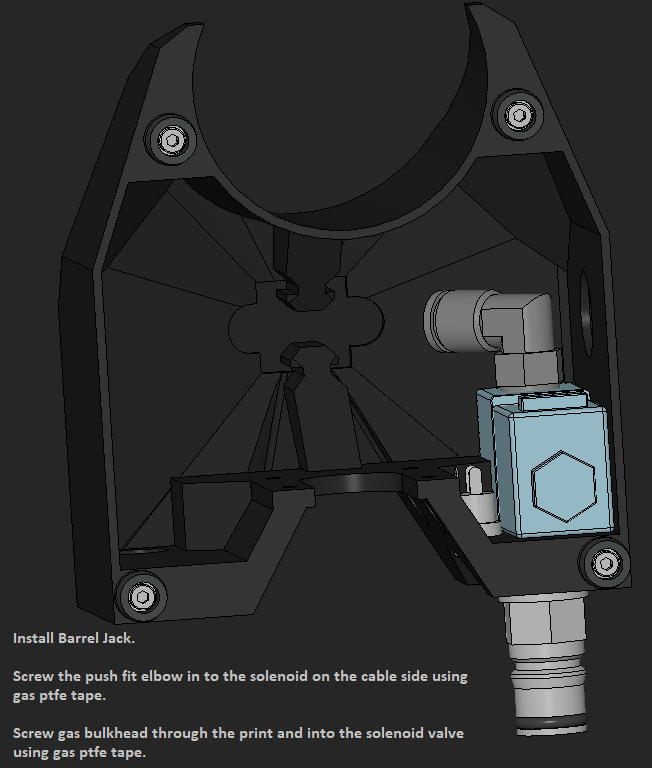
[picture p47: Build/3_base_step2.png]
<br/>
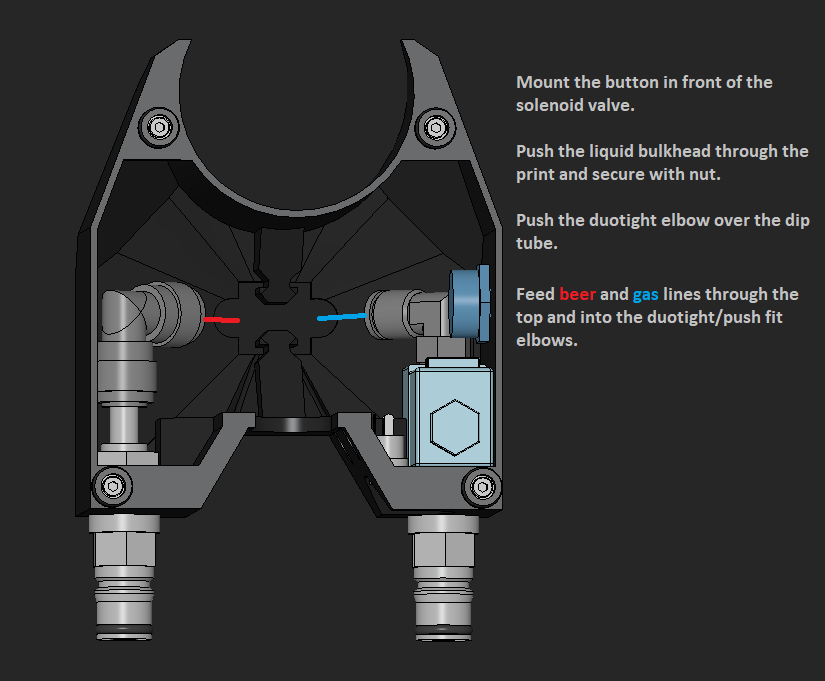
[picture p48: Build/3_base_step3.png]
<br/>
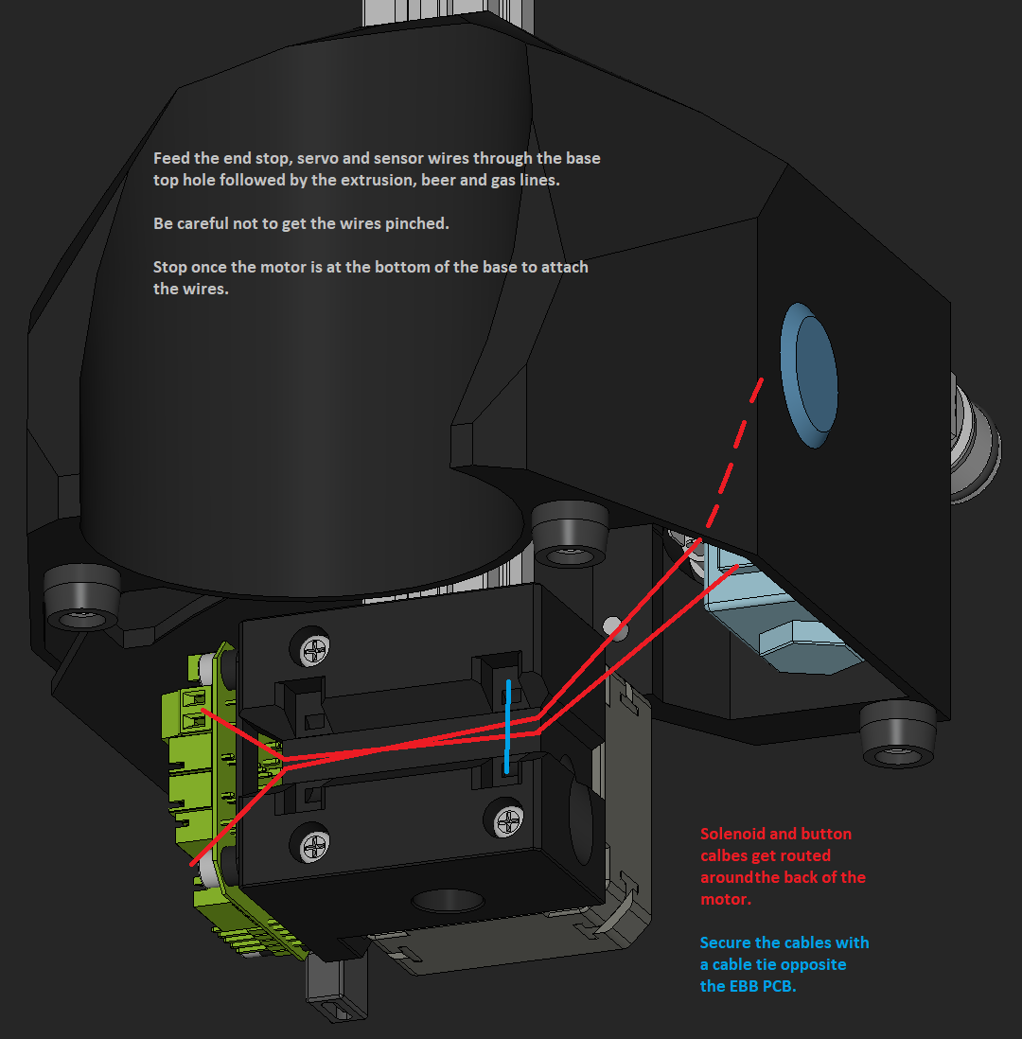
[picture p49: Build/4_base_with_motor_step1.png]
<br/>
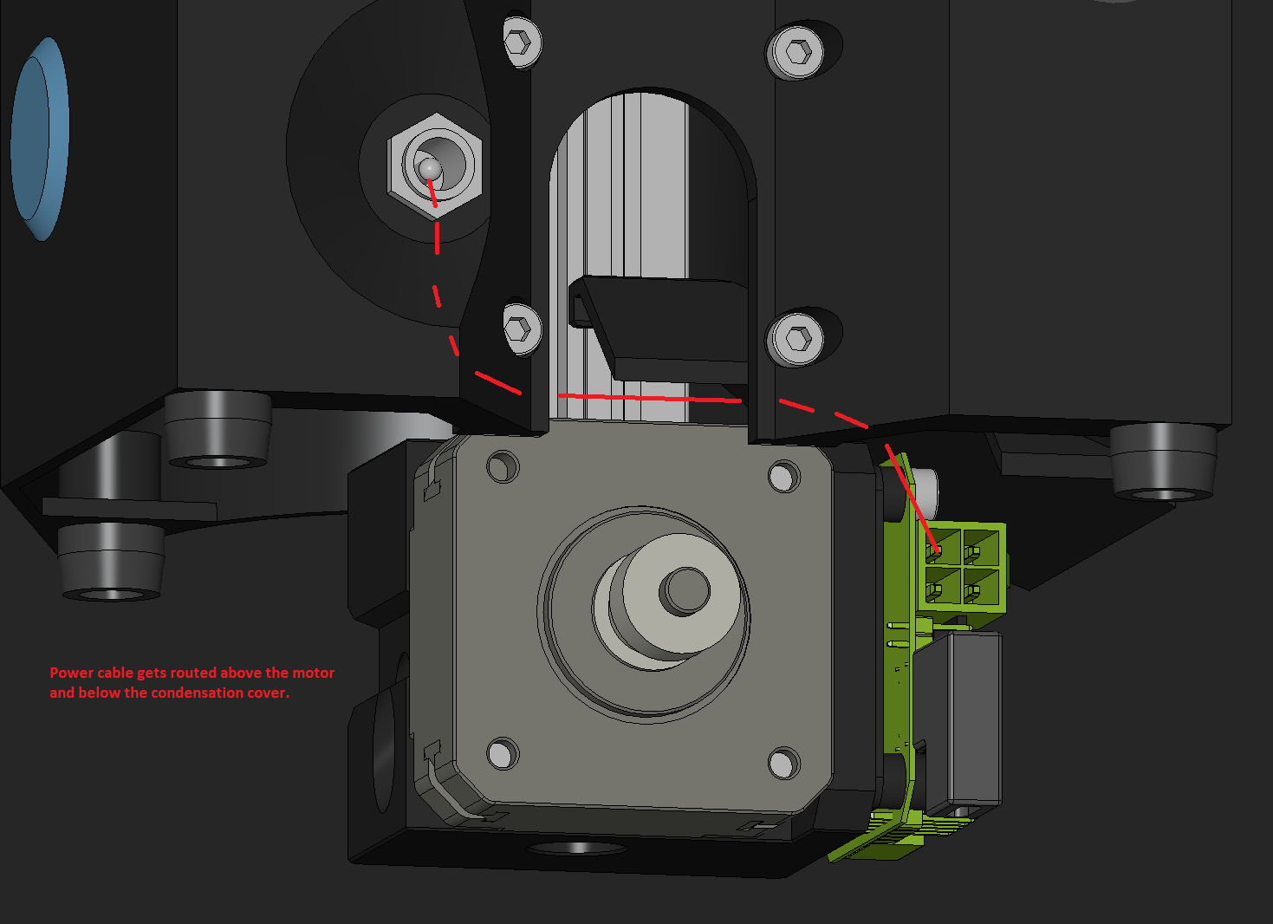
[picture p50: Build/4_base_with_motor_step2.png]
<br/>
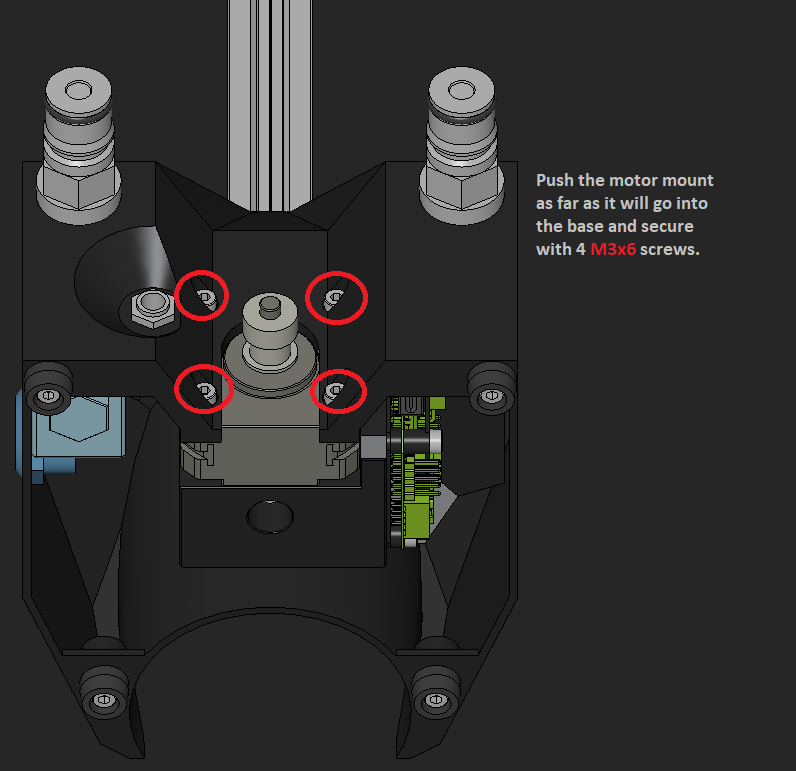
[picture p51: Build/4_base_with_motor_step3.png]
<br/>
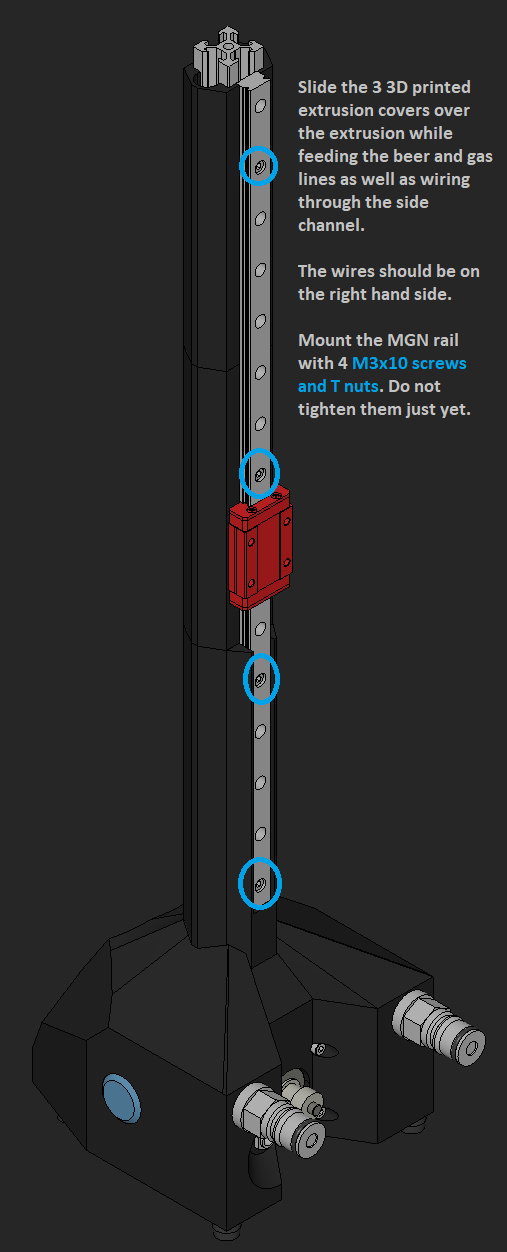
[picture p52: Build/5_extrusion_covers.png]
<br/>
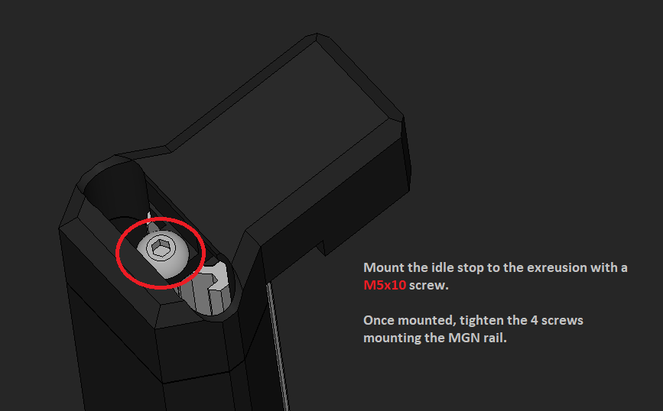
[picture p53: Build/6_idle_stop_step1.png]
<br/>
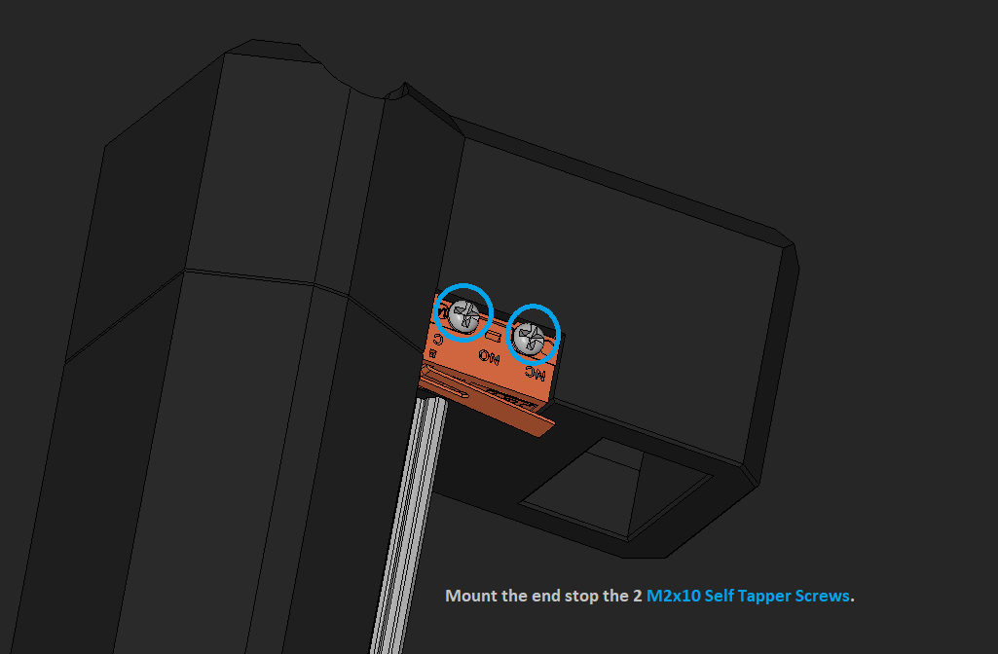
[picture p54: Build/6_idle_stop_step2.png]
<br/>
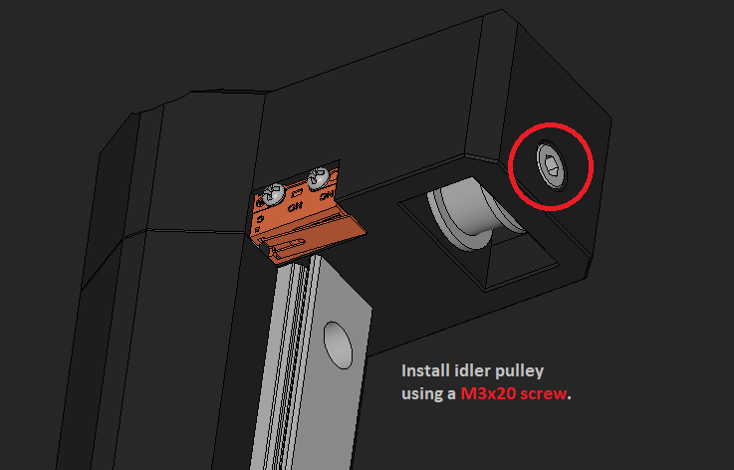
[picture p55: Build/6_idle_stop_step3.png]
<br/>
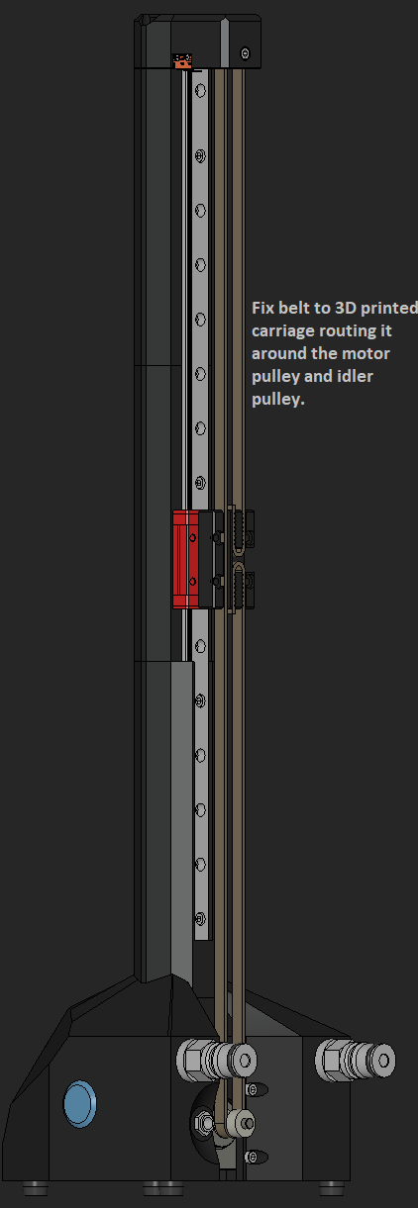
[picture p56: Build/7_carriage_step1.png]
<br/>
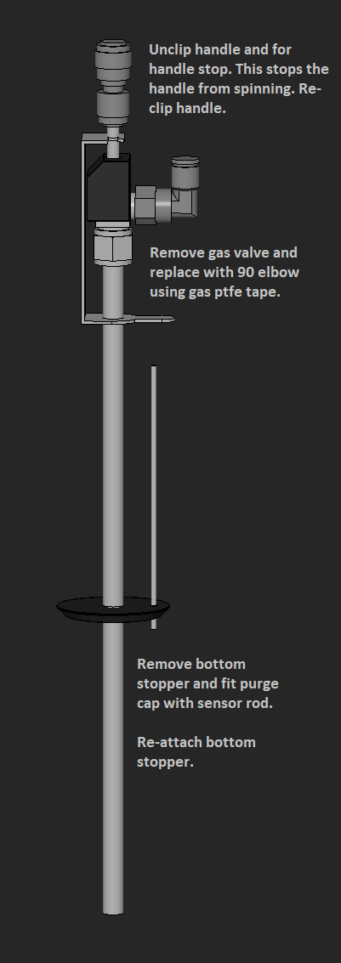
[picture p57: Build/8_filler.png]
<br/>
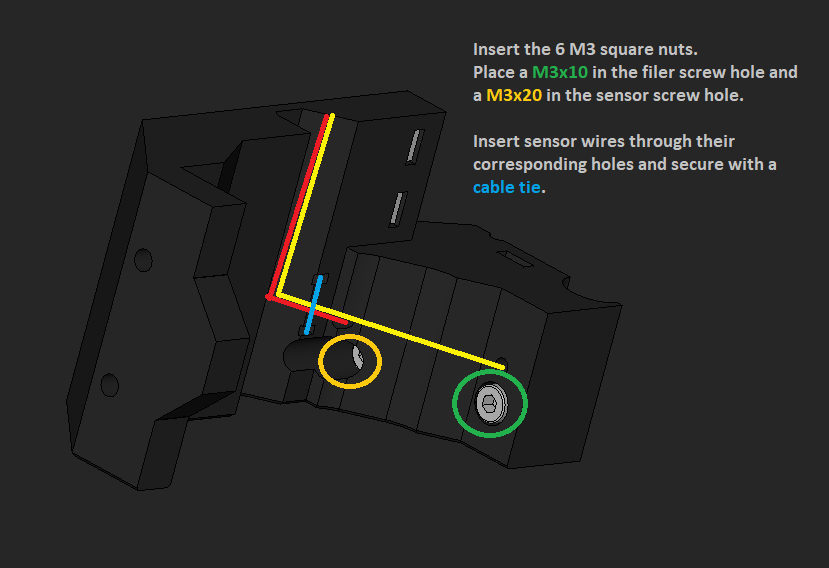
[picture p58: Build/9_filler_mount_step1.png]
<br/>
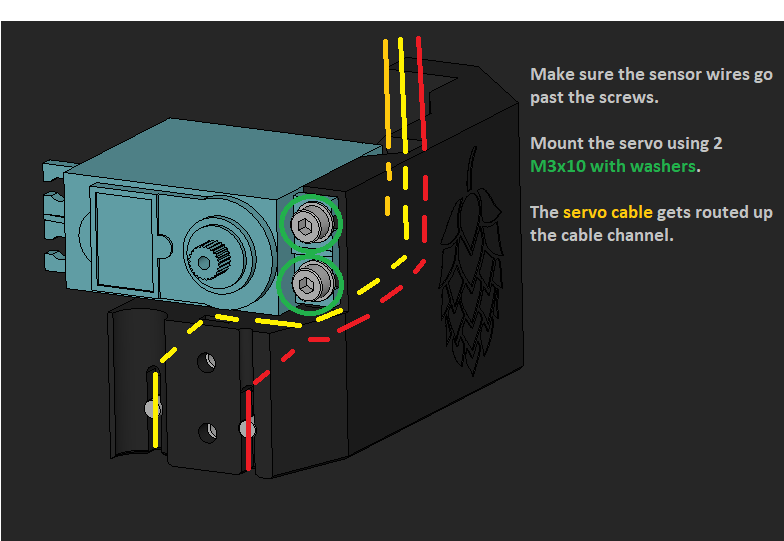
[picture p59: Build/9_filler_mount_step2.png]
<br/>
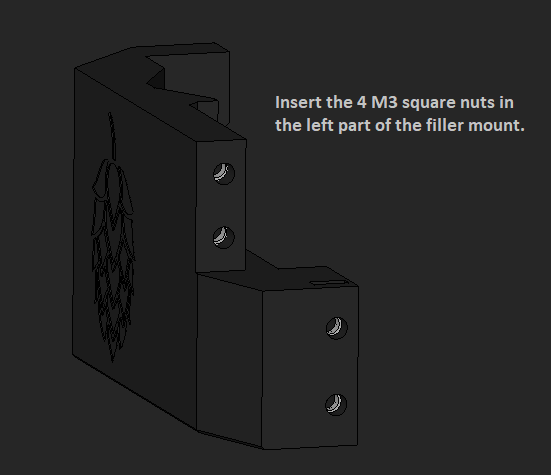
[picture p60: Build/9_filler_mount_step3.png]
<br/>
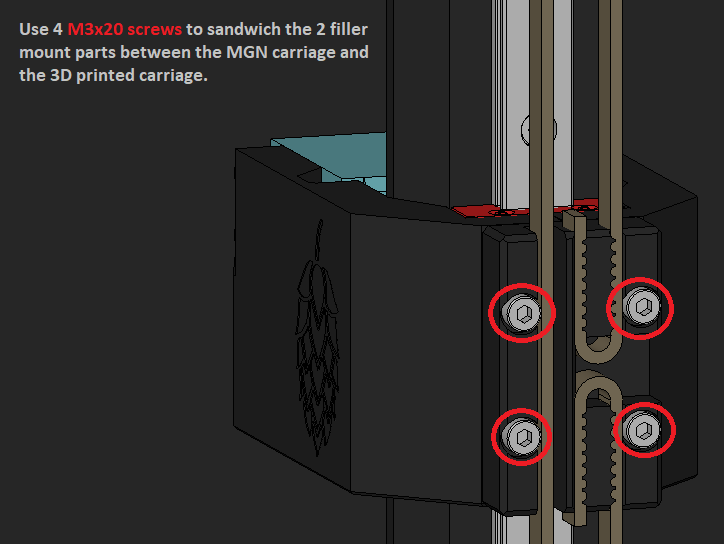
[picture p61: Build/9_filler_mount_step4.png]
<br/>
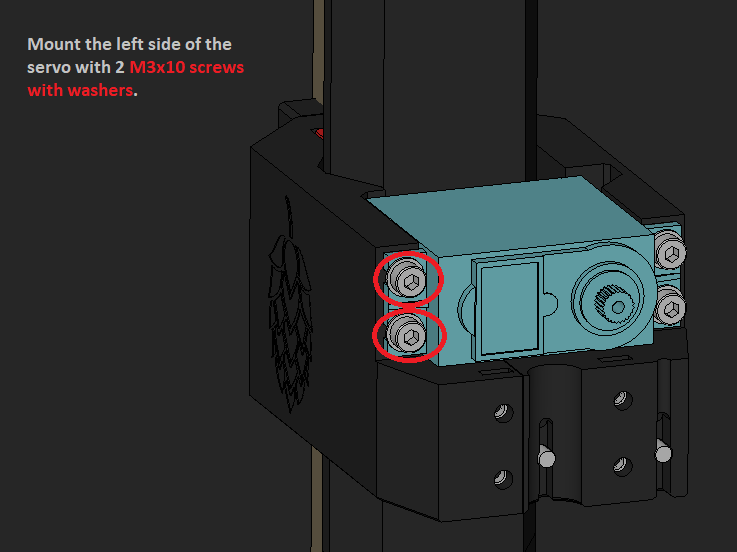
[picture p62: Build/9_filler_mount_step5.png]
<br/>
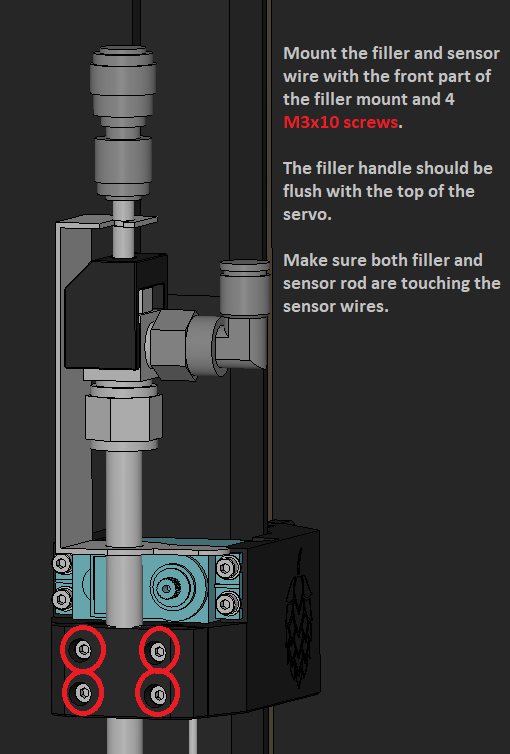
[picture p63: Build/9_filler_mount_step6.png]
<br/>
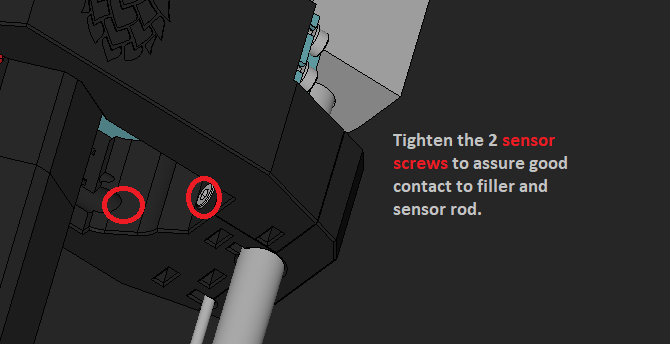
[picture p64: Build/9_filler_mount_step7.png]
<br/>
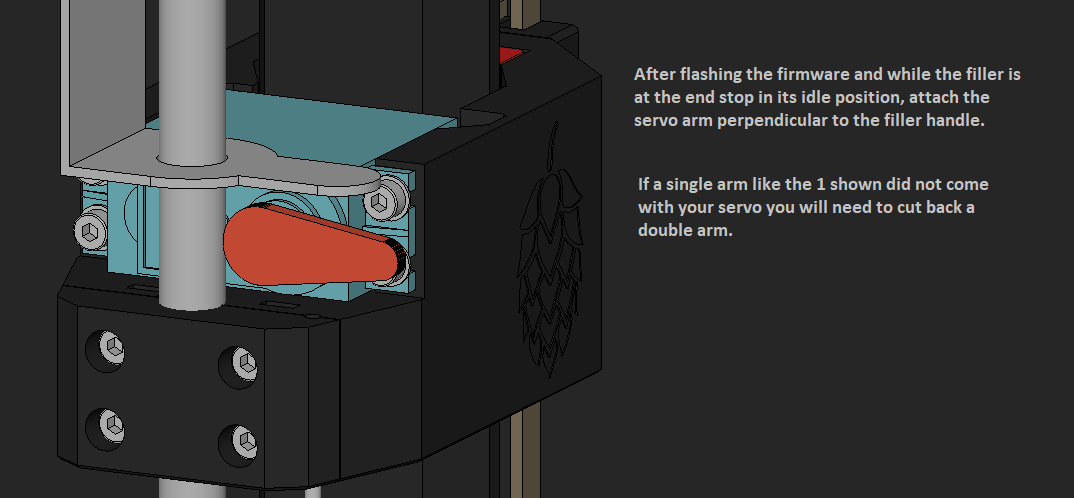
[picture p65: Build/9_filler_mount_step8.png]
<br/>
<br/>

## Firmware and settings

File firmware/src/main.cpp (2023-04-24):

/*
    Filler3 open source can filler
    Copyright (C) 2023  David Gray https://github.com/N3MI-DG

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
    You should have received a copy of the GNU General Public License
    along with this program.  If not, see <https://www.gnu.org/licenses/>.
 */

#include <Arduino.h>
#include <Servo.h>
#include <AccelStepper.h>

#include "UserConfig.h"

Servo servo;
AccelStepper stepper(AccelStepper::DRIVER, STEPPER_STEP, STEPPER_DIR);

enum states {
    MOVE_HOME,
    HOME,
    MOVE_PRE_PURGE,
    PRE_PURGE,
    MOVE_FILL,
    FILLING,
    POST_FILL,
    MOVE_POST_PURGE,
    POST_PURGE
};

states fillerState     = MOVE_HOME;
int currentDestination = 0;
int previousPress      = 0;
int ledValue           = 0;
int ledPrevious        = 0;
int ledPeriodFill      = 10;
int ledTimeFill        = ledPeriodFill - 1;
int ledPeriodFull      = 500;
int ledTimeFull        = ledPeriodFull - 1;

// Pre defined led breathe values because fancy math is expensive
float ledArray[360] = {
0.00, 0.02, 0.08, 0.17, 0.31, 0.48, 0.70, 0.95, 1.24, 1.56, 1.93, 2.33, 2.78, 3.26, 3.77, 4.33, 4.92, 5.55, 
6.22, 6.92, 7.66, 8.44, 9.25, 10.10, 10.98, 11.90, 12.85, 13.84, 14.87, 15.92, 17.01, 18.14, 19.30, 20.49, 
21.71, 22.97, 24.26, 25.57, 26.92, 28.30, 29.71, 31.15, 32.62, 34.12, 35.64, 37.20, 38.78, 40.39, 42.02, 
43.68, 45.37, 47.08, 48.81, 50.57, 52.35, 54.16, 55.98, 57.83, 59.70, 61.59, 63.50, 65.43, 67.38, 69.34, 
71.33, 73.33, 75.34, 77.38, 79.43, 81.49, 83.56, 85.65, 87.76, 89.87, 91.99, 94.13, 96.28, 98.43, 100.60, 
102.77, 104.95, 107.13, 109.33, 111.52, 113.73, 115.93, 118.14, 120.35, 122.57, 124.78, 127.00, 129.22, 131.43, 
133.65, 135.86, 138.07, 140.28, 142.48, 144.67, 146.87, 149.05, 151.23, 153.40, 155.57, 157.72, 159.87, 162.01, 
164.13, 166.25, 168.35, 170.44, 172.51, 174.58, 176.62, 178.66, 180.67, 182.67, 184.66, 186.62, 188.57, 190.50, 
192.41, 194.30, 196.17, 198.02, 199.84, 201.65, 203.43, 205.19, 206.92, 208.63, 210.32, 211.98, 213.61, 215.22, 
216.80, 218.36, 219.88, 221.38, 222.85, 224.29, 225.70, 227.08, 228.43, 229.75, 231.03, 232.29, 233.51, 234.70, 
235.86, 236.99, 238.08, 239.13, 240.16, 241.15, 242.10, 243.02, 243.90, 244.75, 245.56, 246.34, 247.08, 247.78, 
248.45, 249.08, 249.67, 250.23, 250.75, 251.22, 251.67, 252.07, 252.44, 252.76, 253.05, 253.30, 253.52, 253.69, 
253.83, 253.92, 253.98, 254.00, 253.98, 253.92, 253.83, 253.69, 253.52, 253.30, 253.05, 252.76, 252.44, 252.07, 
251.67, 251.22, 250.74, 250.23, 249.67, 249.08, 248.45, 247.78, 247.08, 246.34, 245.56, 244.75, 243.90, 243.02, 
242.10, 241.15, 240.16, 239.13, 238.08, 236.99, 235.86, 234.70, 233.51, 232.29, 231.03, 229.75, 228.43, 227.08, 
225.70, 224.29, 222.85, 221.38, 219.88, 218.36, 216.80, 215.22, 213.61, 211.98, 210.32, 208.63, 206.92, 205.19, 
203.43, 201.65, 199.84, 198.02, 196.17, 194.30, 192.41, 190.50, 188.57, 186.62, 184.66, 182.67, 180.67, 178.66, 
176.62, 174.57, 172.51, 170.44, 168.35, 166.25, 164.13, 162.01, 159.87, 157.72, 155.57, 153.40, 151.23, 149.05, 
146.87, 144.67, 142.48, 140.27, 138.07, 135.86, 133.65, 131.43, 129.22, 127.00, 124.78, 122.57, 120.35, 118.14, 
115.93, 113.72, 111.52, 109.32, 107.13, 104.95, 102.77, 100.60, 98.43, 96.28, 94.13, 91.99, 89.87, 87.75, 85.65, 
83.56, 81.49, 79.42, 77.38, 75.34, 73.33, 71.33, 69.34, 67.38, 65.43, 63.50, 61.59, 59.70, 57.83, 55.98, 54.16, 
52.35, 50.57, 48.81, 47.08, 45.37, 43.68, 42.02, 40.39, 38.78, 37.20, 35.64, 34.12, 32.62, 31.15, 29.71, 28.30, 
26.92, 25.57, 24.25, 22.97, 21.71, 20.49, 19.30, 18.14, 17.01, 15.92, 14.87, 13.84, 12.85, 11.90, 10.98, 10.10, 
9.25, 8.44, 7.66, 6.92, 6.22, 5.55, 4.92, 4.33, 3.77, 3.25, 2.78, 2.33, 1.93, 1.56, 1.24, 0.95, 0.70, 0.48, 0.31, 
0.17, 0.08, 0.02
};


// Set direction based on REVERSE_STEPPER variable
void setDestination(int pos) {
    if (REVERSE_STEPPER) { currentDestination = -pos; }
    else                 { currentDestination =  pos; }
}


// End stop function
void setHome() {
    if (fillerState == MOVE_HOME) {
        fillerState = HOME;
        stepper.setCurrentPosition(0);

        if (digitalRead(PURGE_SOLENOID) == HIGH) { digitalWrite(PURGE_SOLENOID, LOW); } // Close solenoid
    }
}


// User button interrupt function
void userButtonCallBack() {
    if ((millis() - previousPress) > BUTTON_DEBOUNCE) {
        // Move to pre purge if at home position while user button pressed
        if (fillerState == HOME) { fillerState = MOVE_PRE_PURGE; }

        else if (fillerState == POST_FILL) {
            if (POST_PURGE_DURATION > 0) { fillerState = MOVE_POST_PURGE; }
            else                         { fillerState = MOVE_HOME; }
        }

        // Activate emergency stop is user button is pressed while state is not HOME or POST_FILL
        else {
            servo.write(SERVO_POS_IDLE);       // Move servo to idle position
            digitalWrite(PURGE_SOLENOID, LOW); // Disable solenoid
            fillerState = MOVE_HOME;           // Change back to default state

            HAL_NVIC_SystemReset();            // Reset the device (Nasty but it works)
        }
    }

    previousPress = millis();
}


// LED filling timer function
void ledCallBack(void) {
    if (fillerState == FILLING) {
        ledTimeFill++;

        if (ledTimeFill == ledPeriodFill) {
            if (ledValue == 360) { ledValue = 0; }
            else                 { ledValue++;   }

            analogWrite(USER_LED, ledArray[ledValue]);
            ledTimeFill = 0;
        }
    }

    else if (fillerState == POST_FILL) {
        ledTimeFull++;

        if (ledTimeFull == ledPeriodFull) {
            if (!ledValue == 0)   { ledValue = 0;   }
            else                  { ledValue = 255; }

            analogWrite(USER_LED, ledValue);
            ledTimeFull = 0;
        }
     }

    else { analogWrite(USER_LED, 255); }
}


void setup() {
    servo.attach(SERVO_SIGNAL);  // Attach servo
    servo.write(SERVO_POS_IDLE); // Move servo to idle position

    // Setup IO
    pinMode(END_STOP,       INPUT);
    pinMode(USER_BUTTON,    INPUT);
    pinMode(FILL_SENSOR,    INPUT);
    pinMode(USER_LED,       OUTPUT);
    pinMode(STEPPER_ENABLE, OUTPUT);
    pinMode(PURGE_SOLENOID, OUTPUT);

    digitalWrite(PURGE_SOLENOID, LOW); // Disable solenoid
    digitalWrite(STEPPER_ENABLE, LOW); // Enable stepper motor

    // Set stepper speeds
    stepper.setMaxSpeed(STEPPER_MAX_SPEED);
    stepper.setAcceleration(STEPPER_ACCELERATION);

    // Setup and attach User button timer interrupt
    TIM_TypeDef   *userInstance = TIM1;
    uint32_t       userChannel  = 3;
    HardwareTimer *userTimer    = new HardwareTimer(userInstance);

    userTimer->setMode(userChannel, TIMER_INPUT_CAPTURE_FALLING, USER_BUTTON);
    userTimer->attachInterrupt(userChannel, userButtonCallBack);
    userTimer->resume();

    // Setup and attach LED timer
    TIM_TypeDef   *ledInstance = TIM2;
    HardwareTimer *ledTimer    = new HardwareTimer(ledInstance);

    ledTimer->setOverflow(10, HERTZ_FORMAT);
    ledTimer->attachInterrupt(ledCallBack);
    ledTimer->resume();

}


void loop() {
    switch(fillerState) {
        case MOVE_HOME:
            if (!stepper.run()) {
                if (currentDestination == 0) { stepper.setCurrentPosition(FILL_POSITION - 750); } // Assume machine starts at its limit (fill position - a little bit)

                setDestination(50);                                                               // Set destination just a little past home
                stepper.moveTo(currentDestination);                                               // Start moving home
            }

            if (digitalRead(END_STOP) == END_STOP_TRIGGER) { 
                setHome();

                if (PURGE_TRAVEL_MOVES) { digitalWrite(PURGE_SOLENOID, LOW); }                    // Close solenoid
            }
            else { stepper.run(); }

            break;

        case HOME:
            break;

        case MOVE_PRE_PURGE:
            // If Idle, start moving
            if (!stepper.run()) {
                setDestination(PRE_PURGE_POSITION);
                stepper.moveTo(currentDestination);
            }

            // When destination reached, change state to pre purge
            if (stepper.currentPosition() == currentDestination) { fillerState = PRE_PURGE; }

            stepper.run();
            break;

        case PRE_PURGE:
            digitalWrite(PURGE_SOLENOID, HIGH);                             // Open Solenoid
            delay(PRE_PURGE_DURATION);                                      // Wait for pre purge
            
            if (!PURGE_TRAVEL_MOVES) { digitalWrite(PURGE_SOLENOID, LOW); } // Close solenoid

            fillerState = MOVE_FILL;                                        // Change state to move fill
            break;

        case MOVE_FILL:
            // If Idle, start moving
            if (!stepper.run()) {
                setDestination(FILL_POSITION);
                stepper.moveTo(currentDestination);
            }

            // When destination reached, change state to filling
            if (stepper.currentPosition() == currentDestination) {
                if (PURGE_TRAVEL_MOVES) { digitalWrite(PURGE_SOLENOID, LOW); } // Close solenoid

                fillerState = FILLING;
            }

            stepper.run();
            break;

        case FILLING:
            // While filling continuously poll sensor
            if (servo.read() >= SERVO_POS_FILL) {

                // When full
                if (analogRead(FILL_SENSOR) < SENSOR_TRIGGER) {
                    servo.write(SERVO_POS_IDLE);  // Return servo to idle position

                    if (POSITIVE_PRESSURE)            { fillerState = POST_FILL;       }
                    else if (POST_PURGE_DURATION > 0) { fillerState = MOVE_POST_PURGE; }
                    else                              { fillerState = MOVE_HOME;       }
                }
            }

            else { servo.write(SERVO_POS_FILL); } // Move servo to fill position and start filling

            break;

        case POST_FILL:
            break;

        case MOVE_POST_PURGE:
            // If Idle, start moving
            if (!stepper.run()) {
                setDestination(POST_PURGE_POSITION);
                stepper.moveTo(currentDestination);
            }

            // When destination reached, change state to post purge
            if (stepper.currentPosition() == currentDestination) { fillerState = POST_PURGE; }

            stepper.run();
            break;

        case POST_PURGE:
            digitalWrite(PURGE_SOLENOID, HIGH); // Open solenoid
            delay(POST_PURGE_DURATION);         // Wait for post purge

            if (!PURGE_TRAVEL_MOVES) { digitalWrite(PURGE_SOLENOID, LOW); } // Close solenoid

            fillerState = MOVE_HOME;            // Change state to move home
            break;

    }
}

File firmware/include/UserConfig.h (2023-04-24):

/*
    Filler3 open source can filler
    Copyright (C) 2023  David Gray https://github.com/N3MI-DG

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
    You should have received a copy of the GNU General Public License
    along with this program.  If not, see <https://www.gnu.org/licenses/>.
 */

#include <Arduino.h>

/* Pins */
// EBB42 https://raw.githubusercontent.com/bigtreetech/EBB/master/EBB%20CAN%20V1.1%20(STM32G0B1)/EBB42%20CAN%20V1.1/Hardware/EBB42%20CAN%20V1.1%26V1.2-PIN.png
// EBB36 https://raw.githubusercontent.com/bigtreetech/EBB/master/EBB%20CAN%20V1.1%20(STM32G0B1)/EBB36%20CAN%20V1.1/Hardware/EBB36%20CAN%20V1.1%26V1.2-PIN.png

#define END_STOP             PB8
#define USER_BUTTON          PB6
#define USER_LED             PA1 // FAN1 PA0, FAN2 PA1
#define FILL_SENSOR          PA3

#define PURGE_SOLENOID       PA2 // EBB V1.1 PA2, EBBV1.2 PB13
#define SERVO_SIGNAL         PB9
#define STEPPER_STEP         PD0
#define STEPPER_DIR          PD1
#define STEPPER_ENABLE       PD2


/* Variables */
#define BUTTON_DEBOUNCE      200    // Debounce in ms
#define SENSOR_TRIGGER       400    // Analog trigger between 0 to 4095 (lower is more sensitive)
#define PRE_PURGE_DURATION   3000   // Pre purge duration in ms
#define POST_PURGE_DURATION  0      // Post purge duration in ms
#define PRE_PURGE_POSITION   -10550 // Relative steps from end stop to pre purge position
#define POST_PURGE_POSITION  -3000  // Relative steps from end stop to post purge position
#define FILL_POSITION        -10800 // Relative steps from end stop to filling position
#define SERVO_POS_IDLE       0      // Servo position while idle
#define SERVO_POS_FILL       60     // Servo position while filling
#define STEPPER_MAX_SPEED    10000  // Stepper max speed in steps per second
#define STEPPER_ACCELERATION 24000  // Stepper acceleration in steps per second per second
#define REVERSE_STEPPER      false  // Reverse stepper direction
#define END_STOP_TRIGGER     HIGH   // End stop trigger state (NO = HIGH, NC = LOW)
#define PURGE_TRAVEL_MOVES   true   // Continue to purge while moving to the next position after purge position
#define POSITIVE_PRESSURE    false  // After filling the gantry will stay at the fill position until user button is pressed

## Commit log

2023-04-06 Initial Release
    [17HS08-1004S.stp, BOM.csv, Base.stl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]
2023-04-24 Add purge while moving and positive pressure mode

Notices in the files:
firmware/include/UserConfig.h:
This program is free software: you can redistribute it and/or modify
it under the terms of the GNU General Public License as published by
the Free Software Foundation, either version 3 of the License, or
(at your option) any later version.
